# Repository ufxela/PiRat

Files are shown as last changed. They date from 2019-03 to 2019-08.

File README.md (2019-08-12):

# Pi Rat!

**Take a look at the video_links.md file in the images folder to see some videos 
of the robot in action!**

## Project Description

### Introduction
The Pi Rat is a robot that can solve a maze autonomously. It does this with two abilities: 
sensing and movement. Sensing comes through the form of an ultrasonic sensor (which is mounted
on a servo so it can look around) as well as a line follower module. The ultrasonic sensor
detects walls and the line follower module keeps the robot from veering off path (allows the robot
to go straight over long distances without hitting a side wall). The movement abilities come through 
two continuous rotation servos with hall effect sensors to provide rotational feedback. Each of these
has a wheel mounted to them, to create a differential drive car. Also, as I mentioned previously,
there's a servo which pans around to detect walls in combination with the utlrasonic sensor. 

The idea of the Pi Rat is to know as little information as possible about the maze. So far, I've been able
to eliminate the need for where the exit of the maze is, as well as any information about how the maze 
is set up. The information that I still require, and can be elimiated are the following: 
* The wall length / size of the maze
   * can be eliminated by sampling wall sizes with the ultrasonic sensor
* The dimension of the maze
   * With the basic wandering algorithm this actually isn't required information
* The starting position & bearing of the Pi Rat
* The need for a black line under each square of the maze to keep the Pi Rat from veering off path
   * Can use the ultrasonic sensor to measure where the Rat is relative to walls, in order to correct 
     position. Is more complex, however, than having black lines, as there won't always be walls present.

I had the idea for the Pi Rat during parents weekend, when I was talking with my mom and my
dad. My initial impression of the robot was pretty wrong. I thought that it would be able to 
maintain it's position well enough that I wouldn't have to have a line sensor.

Through this project, I've prided doing as much as I can by myself. It's meant that I've gotten the 
opportunity to learn new, unexpected things, like 3D modelling with CAD, laser cutting and 3D printing. 
I've also learned that I suck at painting (I can't paint straight, clean lines haha).

My junior year of high school, I tried to control servos with a Raspberry Pi running an OS. I quickly discovered
that this was not as straightforward as I would wish: apparently, the Raspberry Pi wasn't able perform time
sensitive actions well. I'm really glad that I've been able to come back to that and be able to control servos
with the Raspberry Pi with no extraneous hardware helping me.

### The Steps

The work I've done in this project can be broken down into bit sized steps. In approcimate cronological 
order for each category of work (I did software and hardware simultaneously): 

**Software**
1. Write a module to interface with the ultrasonic module 
1. Write a module to output pwm signals
1. Write a module to read pwm inputs
1. Write a module to control servos with the pwm output module
1. Write a module to control continuous rotation servos with the pwm output module
1. Write a module to interface with the line detecting sensor
1. Write a module to provide for basic differential drive car controls
1. Write a module to bundle all of the Pi Rat sensing into a single unified location
1. Write a module to bundle all Pi Rat movements into a single unified location, also add 
   movement correction, to ensure the Pi Rat is properly oriented
1. Write a module to use Pi Rat sensing and movement modules as well as maze solving algorithms
   to create functions which provide the robot with it's highest level of functionality
1. Combine everything neatly with a button which can be used to start / stop Pi Rat maze solving.

**Hardware**
1. Design Pi Rat robot chassis & 3D print it
1. Create a maze
   1. For portability, uses laser cut & self designed wall holder posts
   1. For walls, uses cut manilla folders which slot into wall holder posts
   1. For the ground, used a giant sheet of paper with a painted grid. 

### The Steps, in More Detail

**Software**
1. *Write a module to interface with the ultrasonic module:* This was relatively simple, doesn't 
   use interrupts. I referenced Pat's ultrasonic code. Initially, this function returned values in 
   inches. However, I wanted more accuracy, so I changed that to microseconds. One big issue I've had 
   with the ultrasonic sensor is the power line coming out, and making me think that my maze solving
   algorithms were broken. Make sure everything's plugged in!
1. *Write a module to output pwm signals:* This was one of the more challenging modules to write. I used
   interrupts to do it. My initial strategy was to step a timer up, and have thresholds where if a timer step
   counter was past that threshold, the output would switch. It ended up hogging up all CPU time, but I think
   it may be because I forgot to clear timer events. Regardless, I ended up switching to the current strategy
   of taking up 4 ms of every 20 ms of CPU time for a dedicated PWM output period. Bit banging. 
1. *Write a module to read pwm inputs:* This was an easy module to write initially, but some bad planning came
   back to bite me. The initial problem was that since pwm outputs hogged a big chunk of CPU time, if inputs
   clashed with outputs, bad things would happen. I fixed this by timing input reads around outputs. Another issue
   here was I forgot to ground things.
1. *Write a module to control servos with the pwm output module:* pretty straightforward, just tedious. 
1. *Write a module to control continuous rotation servos with the pwm output module:* A regret that I have is
   not leveraging the servo control module to make this. If I care enough in the future, I may fix this, but it
   functions perfectly right now. 
1. *Write a module to interface with the line detecting sensor:* Pretty straight forward, as I had the reference 
   from the manufacturer which included Arduino code. 
1. *Write a module to provide for basic differential drive car controls* This was one of the harder modules to
   write. The issue was that going straight means you need to move each wheel the same amount at the same speed.
   This is difficult when you use continuous rotation servos, which by nature are very inaccurate. Luckily, my
   continuous rotation servos had rotary encoders which made straight forward motion actually possible. However,
   I had to change my strategy for moving forward to a more complex one in order to get things working well.
1. *Write a module to bundle all of the Pi Rat sensing into a single unified location* Pretty straight forward. Uses
   a couple of different methods to filter through data from sensors, to make sure they're accurate. A problem is
   if a line is right in between two sensors of the line detector, it will hold indefinitely, or at least for a noticable
   time. This can be fixed with a better data getter function.
1. *Write a module to bundle all Pi Rat movements into a single unified location, also add* 
   *movement correction, to ensure the Pi Rat is properly oriented:* This module works really well in its current form.
   To correct forwards motions, it corrects any lateral error as well as angular error based on a measurement it makes 
   before movement as well as a measurement it makes after movement. To correct turns, the Pi Rat will turn, then fix the
   lateral error. These corrections are really nice because it allows for a lot of leeway in the maze design. For example,
   walls don't all have to be the perfect size, as after each turn, any error should be corrected. Furthermore, the turns
   don't have to be perfectly 90 degrees, as the forwards motion correction will soften offsets.
1. *Write a module to use Pi Rat sensing and movement modules as well as maze solving algorithms*
   *to create functions which provide the robot with it's highest level of functionality:* This was the final step
   in my mind, and used my cs106b maze solving knowledge.
1. *Combine everything neatly with a button which can be used to start / stop Pi Rat maze solving:* icing on the cake; to
   the in class demonstration a lot more approacable to interaction. 

**Hardware**
1. *Design Pi Rat robot chassis & 3D print it:* Went through three iterations of design. The first did not account
   for the line follower, as I didn't expect to need it. The second fixed this and the third added additional supports
   between the top and bottom pieces to make the fit cleaner. I really liked the way my chassis turned out. My idea
   behind it was to make it as small as possible, so I could make the maze size as small as possible. I also didn't want
   anything permanent, so there's no glue holding anything together: everthing is friction fit (well, wires are taped down).
   Some things just worked out in the design, like routing the continuous rotation servo's wires, or making sure the 
   wheels fit in the chassis. Also, I got to learn (well, sorta...) fusion 360. I don't say that confidently because all
   I did was make a bunch of rectangles and extrude them to various heights. 
1. *Create a maze:* In fashion with the rest of my project, I wanted to complete this myself. I also wanted it
   to be portable, for convenience. 
   1. *For portability, uses laser cut & self designed wall holder posts:* I designed these in fusion 360, and discovered
   that laser cutters are really scary. I also had to assemble the flat pieces into non-flat structures. I used a lot
   of hot glue for this.
   1. *For walls, uses cut manilla folders which slot into wall holder posts:* Manilla folders are actually an amazing
   building material. I got a bunch super cheap for their conventional purpose, but I had extras, so why not put them to use?
   Fun fact: I prototyped a chassis with only manilla folders, tape and hot glue. 
   1. *For the ground, used a giant sheet of paper with a painted grid:* I painted this, using long manilla folder
   strips to make sure I didn't paint in the wrong places. That ended up not really working because paint got on the
   bottom of those strips, and ended up spreading paint all over, including on my body. As a result, I had to use white paint
   to cover all the black blotches that weren't supposed to be there (on the maze, not my body... thankfully the paint was
   easily washable). 

### The Product
The end result of all of this work was that I had a Pi Rat that can solve a maze in two ways!

The first way is with a really basic algorithm which follows this procedure:
`
for each direction:
  if open:
    go that direction
    recur
`
The nice thing is that this algorithm needs very little information about the maze. The bad thing is that it doesn't work
always. To use this, just call the maze wander function, place the rat in the maze, and watch it solve the maze!

The second way is with a depth first search. This algorithm needs a little more information about the maze, like
where the Pi Rat starts in the maze, and the dimensions of the maze. It always works when there is a path, however. To use 
this, update some constants in main.c (as well as wall lengths in the car control module), then call the maze solver
function and watch as the Pi Rat solves the maze!

The program is for the most part modular: by chaning a few constants, the maze solving is generalizable to 
any rectangular maze of any dimensions, configuration and wall length!

[Video Links!](https://github.com/cs107e/ufxela-project/blob/master/images/video_links.md)

### Pictures! (A Lot More in Images Folder)
The Maze:
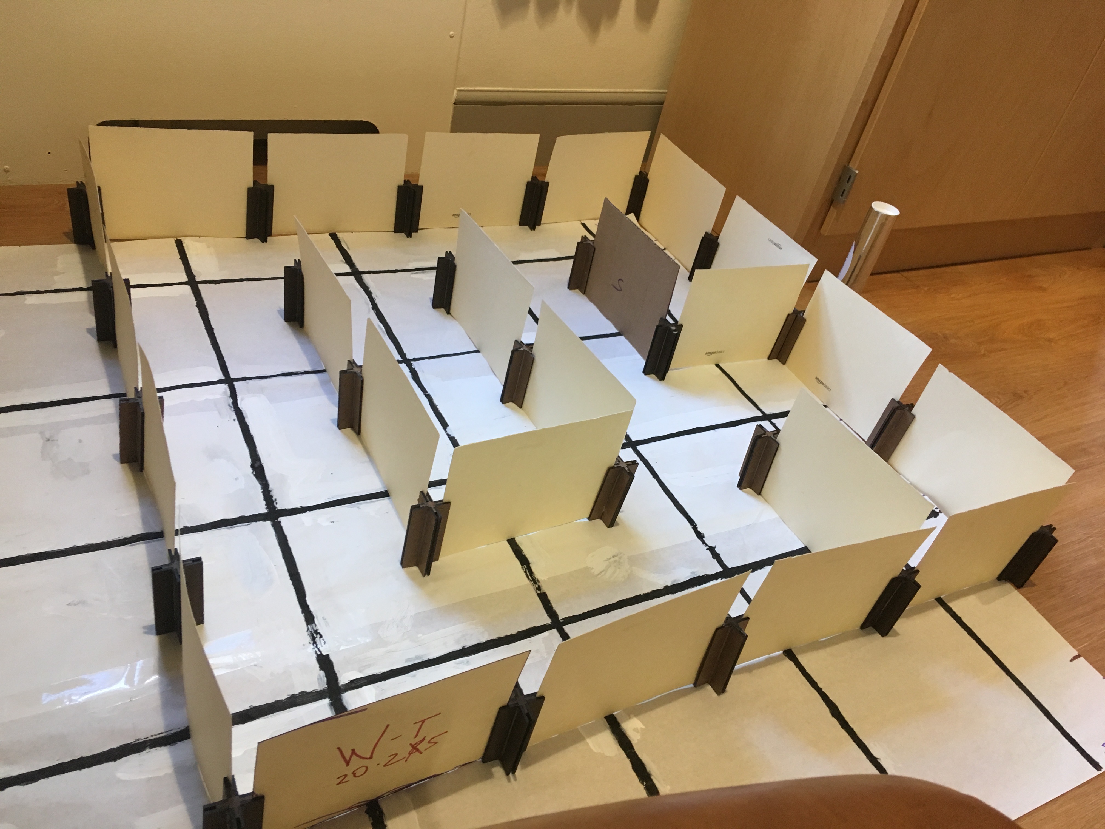
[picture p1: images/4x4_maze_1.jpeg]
The Maze

Another Maze:
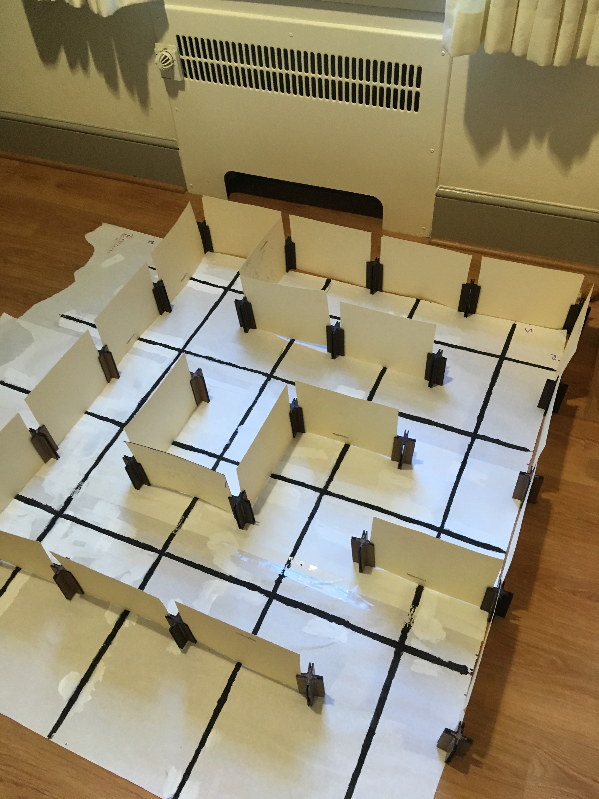
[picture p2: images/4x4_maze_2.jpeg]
Another Maze

The Maze, deconstructed
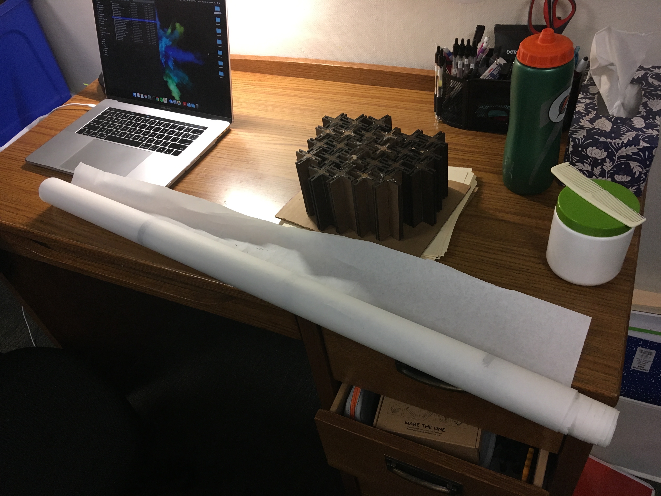
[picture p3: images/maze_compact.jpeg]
Deconstructed Maze

The Pi Rat: 
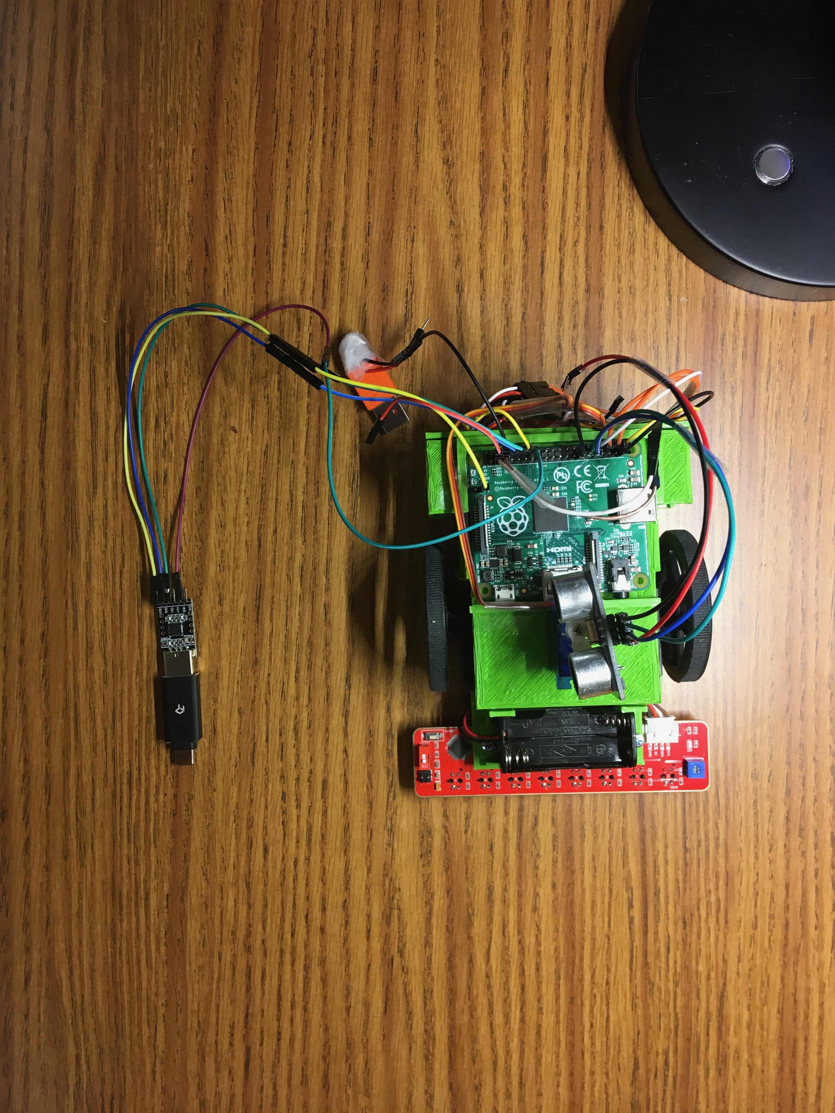
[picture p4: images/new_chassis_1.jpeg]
Pi Rat 1

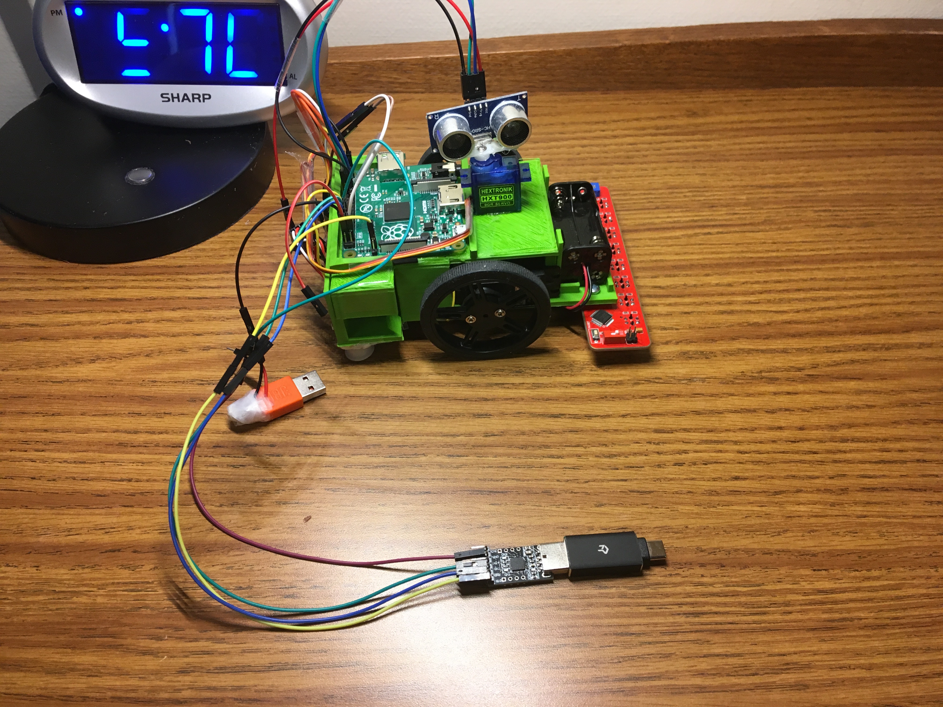
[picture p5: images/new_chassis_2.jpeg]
Pi Rat 2

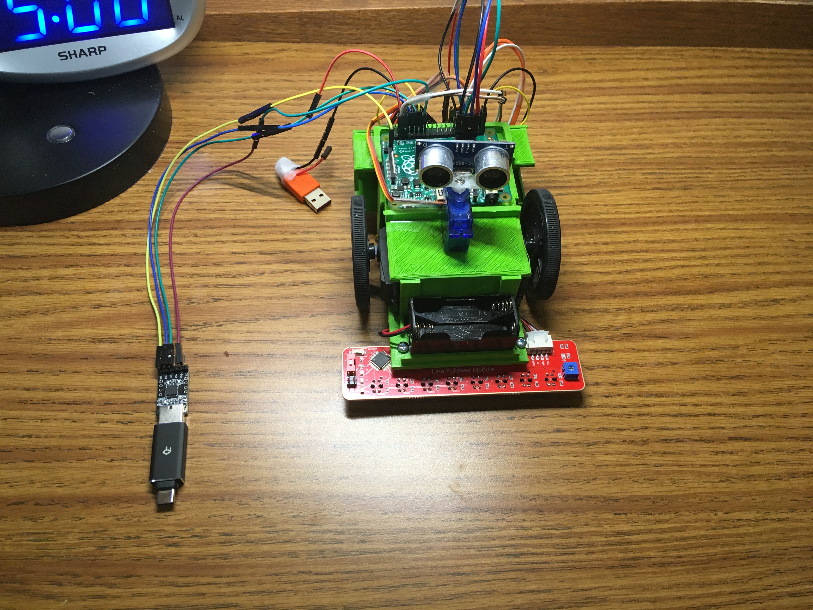
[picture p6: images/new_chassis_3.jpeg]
Pi Rat 3

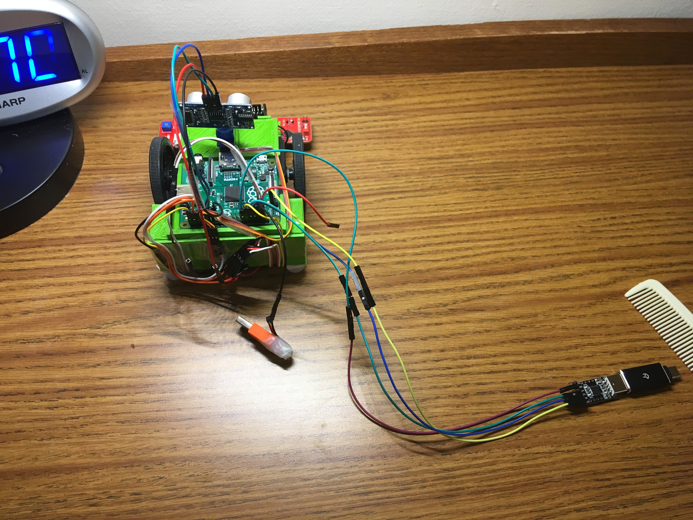
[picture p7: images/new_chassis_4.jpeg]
Pi Rat 4

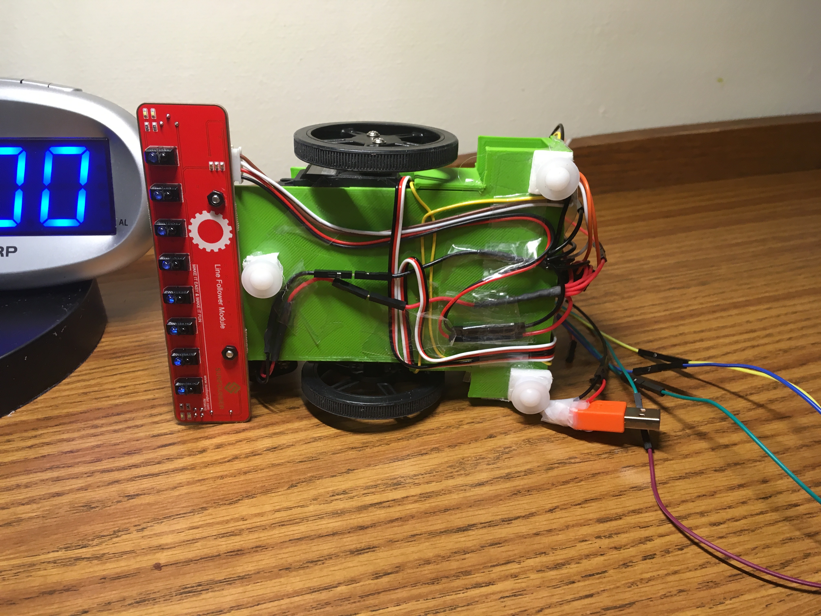
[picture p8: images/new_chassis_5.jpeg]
Pi Rat 5


## Notable Challenges
1. *PWM Outputs:* This was a big hurdle. My first implementation of PWM outputs failed. It seemed to hog all the CPU time.
  I now relaize that I probably wrote it wrong (forgot to clear timer events). I haven't had the effort to check if this is
  why, since the current version works. However, the reason I think this is because, when set to have cycle length 20ms, 
  the actual cycle length turned out to be ~7ms (measured with a logic analyzer). I think this is because the interrupt 
  handler was just being called nonstop. Once I did switch to the current implementation of the code, however, the servos
  still weren't working, even though the logic analyzer showed valid PWM signals. Initially, I thought this was because
  the signals weren't precise enough. However, it turned out that it was because I didn't connect all of my grounds. 
  Throughout the process of solving PWM outputs, Pat helped me a lot. One suggestion he gave me was to use a task queue, which
  although I didn't end up implementing, inspired me to switch to the current implementation of PWM. 
1. *PWM Inputs:* While solving PWM outputs, I reached a point where I felt I was in too deep and couldn't think freshly any
  more, so I switched to solving PWM inputs. My initial implementation of these worked, and I was super excited! Then,
  fifteen minutes later, with no changes to the code, I tried again, and it had stopped working! This was heartbreaking,  
  especially since I wasn't able to get PWM outputs to work. I spent an hour digging through the code, seeing what might
  have gone wrong. This didn't lead anywhere. Then had the idea to physically reconstruct my successful setup exactly,
  to see if that would change anything. It did! It turned out that I didn't connect my ground lines properly. That was
  one of the most confusing hours of this project, and one of the most frustrating.
1. *Going straight & accurately reading wheel positions* These two problems were highly entangled. My inital wheel position
  reader was very imperfect. I regularly got very wonky data from the pwm input reader. My inital strategy to solve this
  was to just deal with it by adding in data filters. This gave limited success, but every once in a while, there was an edge
  case of bad data which would break everything. This meant the wheels would track well for maybe a minute of movement, but
  break after that. I could have added more filters to cover more and more edge cases. Maybe I could have even gotten a 
  perfect filter. However, my filtering code was only getting longer and more convoluted. The right way to do things was to
  dig into the PWM inputs and see why they were so wonky. Once I solved that, I didn't need any filters, and my code worked
  better than ever, with more simplicity than ever. Inaccurate wheel positions also meant that my movements were all wrong.
  At the time, I was simply trying to perfect straight forward movement, so we'll focus on that. My initial implementation of
  forward movement was to spin each wheel independently to a set angle, and assume that each wheel was spinning at the same 
  speed. This failed initially because the poor wheel tracking meant I couldn't consistently bring a wheel to a given angle, 
  without "rotation count slipping" which caused wheels to turn a few rotations too much or too little. Once I solved
  the wheel angles, I thought that would solve the issues with my forward motions. They did not. Although each wheel was set
  to spin a different amount, each wheel span at a different rate, which meant at the end of the motion, one wheel would stop
  and the other would continue spinning. This lead to turning. So I decided to switch to a different, more complex forward
  motion function, which made the wheel throttles dependent on eachother's angles. This worked, after some fine tuning.
  It goes to show that not everything is as simple/straightforward as you may initially think.
1. *DFS maze solver:* Unfortunately, this was not as simple as 106b, mostly because of my own fault. In 106b, our mazes
  had walls being area containing squares, instead of one dimensional lines. We also had better data structures. We also
  didn't have to physically move an object and worry about that. Nor did we have to sense the environment as we went. Now,
  I know I could have written more layers of abstraction early on to resolve these differences. But I am naive and didn't
  anticipate these issues coming up. As a result, my code is very verbose, has some arms length recursion, and is pretty ugly
  overall. Furthermore, I had one big bug in my first draft of the code that took me a while to figure out. The bug was that
  I didn't update the position of the Pi Rat enough, which meant it often thought it was in the wrong spot. As a result,
  when testing, the Pi Rat would seemingly ignore certain paths (and presumably, I'd see it run into walls, if I tested it on
  more mazes). This bug would be simple to fix if everything was simulated on my computer. However, since the Pi Rat was 
  physically solving the maze, visibility of the code and program was terrible while the Pi Rat was in the process of solving
  the maze. This is because while the Pi Rat was solving the maze, it couldn't communicate with my computer and therefore,
  I could only speculate as to what it was thinking. To solve this, I spent a couple of hours playing around with the code
  and then re testing, true to a trial and error approach. However, since I had no idea what the Pi Rat was thinking, this
  was very difficult and ultimately unsuccessful (it did get me closer to the end solution, however). Eventually, I 
  succumbed to using extra long jumper wires to connect the Pi Rat to my computer, and then I basically "walked" the Pi Rat
  by following it through the maze with my computer that was connected to it. It was a funny sight to see, but it worked. I 
  was able to get the data I needed to tell me what I was doing wrong (not updating enough). 

In summary, the hardest part of this assignment was definitely visibility & understanding the hardware.

## Things learned
1. Planning is critical, and possibly the most difficult part of it all. Many modules were easy to implement, aside from
  a few roadbumps (like the ones I talked about above). The hard part was finding the right order to write them in and 
  determining what modules to even have, and what to have inside them. 
1. Do things in the right order: you may find yourself in a situation where you can either
  write tests to debug and make information more transparent and make the mechanisms behind
  things more visible, or you can try to brute force things and try to solve things without 
  that information helping your strategy. Sometimes the latter is faster. However, other times 
  it is not, and it can get very frustrating, because you just feel like you don't know what is
  going on. I have more appreciation for the advice that it's worth your time to write tests
  and make code more visible. Even if it takes 30 minutes, it will save your butt later.
1. Don't change things at the last minute, and if you do, be sure to verify that they don't break anything. The night before the project demos, I did some code cleanup, and ended up changing the Pi Rat's internally kept starting position. This meant that when I placed the Rat in the maze, it thought it was somewhere other than where it actually was. This meant that it thought it solved the maze when really it hadn't. And so the project demo did not go as planned, unfortunately. 
1. Some other things I learned are in my proposal

## Extensions
There were a few things that I had ideas for, and wanted to implement if I had the time, but I never ended up getting to them

Here are a few of them:
1. Remove more information about the maze. I talked more about this above.
1. Make a better interface to the Pi Rat. What if the user could tell the Pi Rat where it's start position should be, 
  with just buttons or something? What if the Pi Rat could display information on a 7 segment display or screen?
1. More maze traversing options: go from point A to point B once a maze is mapped out; after a maze is solved, continually
  traverse the optimal path from start to finish.
1. Remove the line follower sensor completely. Instead use the ultrasonic sensor for all orientation corrections.
1. Move past just mazes and into rooms. Explore a room, kind of line a Roomba. Maybe even keep track of
  data about the room. A simple version of this would be really easy to make. 
1. Remote control abilities, maybe over WiFi?
1. Make a white board robot. I have all of the hardware setup to do this.

## Files
1. Images is a folder which includes photos & a markdown file video_links.md to video links
1. 3d wall plate pi rat maze.stl is a stl file for my wall holder plates. I cut 200 of these out
   (25 wall holders * 8 plates per holder)
1. 8x pi rat maze wall plates.dxf is the file I opened with inkscape on Lab 64's laser cutter computer
   Note that you might need to delete some lines, as some are doubled up (my bad).
1. Chassis_Bottom.stl is the part I 3D printed to make the bottom half of the chassis. I'm not currently
   using this one. 
1. Chassis_Top.stl is the final part I 3D printed to make the top half of the chassis
1. Makefile is self explanatory
1. README is this!
1. better_bottom_chassis.stl is the final part I 3D printed to make the bottom half of chassis
1. car_control_module.c/h provide for basic, non corrective car movements for a differential drive car.
   They use cr_servo_module.c/h and pwm_input_module.c/h
1. cr_servo_module.c/h control continuous rotation servos. Uses pwm_output_module.c/h
1. cstart.c is some code that sets a few things up and calls main
1. libmypi.a is the library I wrote for the first 8 weeks of cs107e
1. line_follower_module.c/h is the module which interfaces with the line follower hardware over i2c
1. main.c is the centerpiece of the program. Contains a lot of test code. 
1. memmap is for linking
1. pi rat maze bottom:top plate 3d.stl is the 3d version of the top/bottom plates of wall holder
1. pi rat maze top:bottom plate.dxf is the inkscape openable file I used to laser cut the wall holder 
   plates
1. pi_rat_control.c/h implement different control functions. Uses pi_rat_movement.c/h and 
   pi_rat_sensing.c/h 
1. pi_rat_movement_module.c is the corrective movement module which moves the car in a way which is 
   specific to the setup of a given maze. Uses car_control_module.c/h and pi_rat_sensing.c/h
1. pi_rat_sensing_module.c/h combines ultrasonic_module.c/h and line_follower_module.c/h into one
   centralized module
1. proposal.md was the description that I wrote up on the first lab for this project, and added to
   as I was working in the first week.
1. pwm_input_module.c/h read in pwm signals through interrupts. Uses pwm_output_module.c/h for proper
   timing
1. pwm_output_module.c/h output pwm signals using timer interrupts
1. servo_module.c/h use pwm_output_module.c/h to make a more intuitive servo control library
1. start.s is the first file that gets called when running
1. ultrasonic_module.c/h interface with the ultrasonic sensor. 
1. updated_bottom_chassis.stl was an internediary between my original bottom chassis and the one I used

## Team member work outline
I did it all myself (with the advice of others, listed below, of course)!

## Resources/Citations

Pat's ultrasonic sensor [sample code](https://github.com/cs107e/cs107e.github.io/blob/master/lectures/Sensors/code/sonar/sonar.c) 

-I used this to get the conversion from microseconds to inches.

[Pseudo code](http://www.robotc.net/wikiarchive/Tutorials/Arduino_Projects/Mobile_Robotics/VEX/Using_encoders_to_drive_straight) for forward motion with wheel angle feedback.
 
 -just followed the pseudo code, adding in limits for wheel throttles and fine tuning for my car

Line follower [example code](http://wiki.sunfounder.cc/index.php?title=Line_Follower_Module)

-borrowed the code pretty much directly

[i2c code](https://github.com/cs107e/cs107e.github.io/blob/master/cs107e/src/i2c.c) to communicate to line follower module

Thanks to Ashwin, Jennifer, Julie, and Pat for providing confidence inspiring guidance throughout my project!

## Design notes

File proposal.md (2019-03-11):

# Pi Rat

**Team members:** Alex Fu

**Description:**
PiRat is loosely inspired by Tolman and Honzik’s psychology experiments (1930) 
in which a live rat was placed in a maze and given the task to find a reward 
(stereotypically cheese) within the maze. PiRat will model the rat, and attempt 
to solve a maze given little prior information about the structure of the maze.

PiRat will have two primary abilities: the first is the ability to move around.
The second is to sense its environment. To move around, the Pi Rat will utilize
continuous rotation servos and a rotary encoder. To sense its environment,
the Pi Rat will use a dinstance sensor (either ultrasonic or time of flight). The
Pi Rat will also use a line sensor to keep it's position/orientation correct, so
that it does not stray off the path and run into the sides of the maze. 

With these two abilities, the PiRat can use a depth first search path finder 
algorithm to navigate through a maze, and find a solution. At the same time, 
the PiRat will keep an internal model of the maze, updating the model with each 
measurement it takes with it’s ultrasonic distance/time of flight sensor. 

One challenge of this project is keeping the Pi Rat's orientation correct throughout
the maze. Because the Pi Rat senses very little about it's environement, it is difficult
for it to truly know where it is (position and bearing) within the maze. Therefore, small
inaccuracies in positioning can avalanche to throw the entire Pi Rat off track. 

**Hardware Required:** 
besides a Raspberry Pi,

* 2x parallax feedback 360 servo motors
* 1x time of flight sensor / ultrasonic distance sensor
* 1x 9g servo
* 1x Line Follower Module
* 3D printed chassis
* 2 wheels, good grip (no slipping!)
* free wheel / low friction knob
* cardboard / foamboard to build maze

**Funds Requested:**

* Optical Time of Flight Sensor: 
    * https://www.amazon.com/Adafruit-VL6180X-Flight-Distance-Ranging/dp/B01N0ODI3Q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
    * $13.99
* 9g servo
    * https://www.amazon.com/DaFuRui-Compatible-Helicopter-Airplane-Controls/dp/B07H3S2Y8Q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
    * $7.89
* Line Follower Module 8 Channel Infrared 
    * $12.99
    * https://www.amazon.com/SunFounder-Follower-Infrared-Detection-STM8S105C4/dp/B01HB5YVUG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
* **Total**
    * $34.67 (but I have a $10 amazon credit!)

**Task Breakdown**

*Software:*

1. Write a module to output PWM signals
1. Write a module to read PWM inputs
1. Write module to setup and control a servo through PWM
1. Write module to setup and control continuous rotation servo through PWM
1. Write module to read PWM communications from Parallax Feedback 360 servos, to determine positioning
1. Either:
   1. Communicate through I2C to optical time of flight sensor
   1. Read/write through GPIO to communicate with ultrasonic distance sensor (This is what I have chosen).
1. Write module to communicate via I2C with the line follower module
   1. Will use libpiextra i2c modules
1. Module to move support basic movement of a continuous rotation servo powered car.
   1. With two independent wheels, we will be able to move forward, backward, turn and shimmy to the left and right
1. Module to support advanced movement for Pi Rat
   1. Will keep track of position of Pi Rat
   1. Will have discretized movements so as to follow maze properly
   1. Will have correctional movements that ensure proper orientation within maze (no roaming off track)
1. Code to use all modules to sense environment and move the rat in response based on
   where it wants to go. 
   1. Internal data structure to represent maze
   1. Algorithm to solve maze
   1. Internal data structure to represent current path, and provide ability to backtrack path.
   1. Way to determine when solution is discovered
   1. Traverse solution (back and forth, like a sentry) once found. 
   1. Once maze map is completed, user may tell Pi Rat to go from point A to point B for any two connected
      points in the maze.
   1. User may input instructions to the Pi Rat beforehand to tell it where to go
1. Extensions:
   1. Code to use modules to traverse a new environment that may not be a maze. 
   1. Code to find shortest path from point A to point B within maze. 
   1. Remove any information about the maze at all (step size, dimensions) and use Pi Rat's sensing abilities
      to determine this information itself. 
   1. Add in remote control abilities. 
   
*Hardware:*

1. Model and 3D print chassis for rat
1. Mount time of flight sensor / ultrasonic distance sensor
1. Mount line follower module
1. Find / make wheels which have really good grip
1. Make maze, ideally with configurability. (slot and fit walls)

**Goals for Next Week**
1. Software steps 1-7
1. Hardware steps 1-4
1. Test movement of Pi Rat and see how accurately it can hold its position
1. Test accuracy of ultrasonic sensor
1. Configure servo motors
1. Configure line follower sensor

**Reference and Resources**

*another document that goes into more detail about my project*

https://docs.google.com/document/d/10EH3p42lqzU2tbl3T3y5yWcG4yZZ02CRSOTUqFnZRl0/edit?usp=sharing

*line follower*

http://wiki.sunfounder.cc/index.php?title=Line_Follower_Module
https://github.com/cs107e/cs107e.github.io/blob/master/cs107e/src/i2c.c
Note: this bad boy can't be powered just through the Pi's GPIO pins. Needs external supply!

*ultrasonic sensor*

https://cdn.sparkfun.com/datasheets/Sensors/Proximity/HCSR04.pdf
https://github.com/cs107e/cs107e.github.io/blob/master/lectures/Sensors/code/sonar/sonar.c

*parallax feedback 360 servos*

https://www.parallax.com/product/900-00360

*servos*

https://learn.sparkfun.com/tutorials/pulse-width-modulation/all

*CS107E Libraries*

https://github.com/cs107e/cs107e.github.io/tree/master/cs107e/src
https://github.com/cs107e/cs107e.github.io/tree/master/cs107e/include

Specifically: gpioextra, interrupts, i2c. 

*Wheels*

The wheels that I'm using are borrowed from this kit: https://www.amazon.com/Geekstory-Feetech-Degree-Continuous-Rotation/dp/B079FRHBTR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

**Lessons that I have Learned**
* Have only one ground. Otherwise, you will pull your hairs out.
* Line follower module needs to be powered externally
* At first glance, things will seem definitely doable. Then once you start doing them, they no longer seem doable.
  But once you complete them, they seem very doable.
* Object oriented programming can be very helpful, but not if you don't do it. I should do it more often in my coding.
* There is a lot more to consider besides the software side of things. For example, an uneven weight distribution
  in the chassis will lead to one wheel having more grip than the other. So have an even weight distribution.
* Many things pop up and make other things hard. For example, keeping the orientation of the Pi Rat correct throughout the
  maze. You have to constantly figure solutions out to these challenges. Many of the best solutions come in the shower.
* Oftentimes, things are difficult because you make them so. It can be good to take a step back, and think: is there a 
  simpler, easier solution to things? This is difficult because you can get caught up in the way you currently want to
  do things, and miss out on otherwise obvious things. For example, when writing PWM outputs, initially I picked up Pat's
  idea (which, now that I look back, should work, if I properly used get_and_clear_event()...) with the incrementing interrupt
  counter. But later, I took a simpler, better approach which is currently implemented. Also, with utilizing the line
  follower, my initial thought was to update the orientation as the Pi Rat moved. But then I realized it would be much 
  simpler if I compartmentalized each operation. First move, then correct the movement. 
* This brings me to: compartmentalizing things means you can do so much more. "Stand on the shoulders of giants" except
  In this case, you are the giant. There are so many details of my code that are critical but I've totally forgotten about
  (well, I could recall them, but it's much easier not having the worry of needing to). And by leaking those details from my
  memory, I've allowed myself to use my mind more completely to solve each task. Whereas, if I chose to mesh everything
  together, either I would be able to do much less in coding, or I would have to spend way more effort achieving it. This
  is part of the reason I chose not to use a task queue for control, and instead opted to compartmentalize PWM outputs, even
  if it meant having that 2-3 ms penalty. 
* When you're doing something completely alone, that you really enjoy, there really is nothing else needed. Although I've
  been really frustrated at times (like before I realized you should connect all your grounds--lesson learned!), and I've
  definitely wished that I had someone along side me helping me solve my problems (in a way, I have--through the course staff)
  but at the end of the day, I'm really glad to have embarked on this project. It's definitely overwhelming. But worth it.

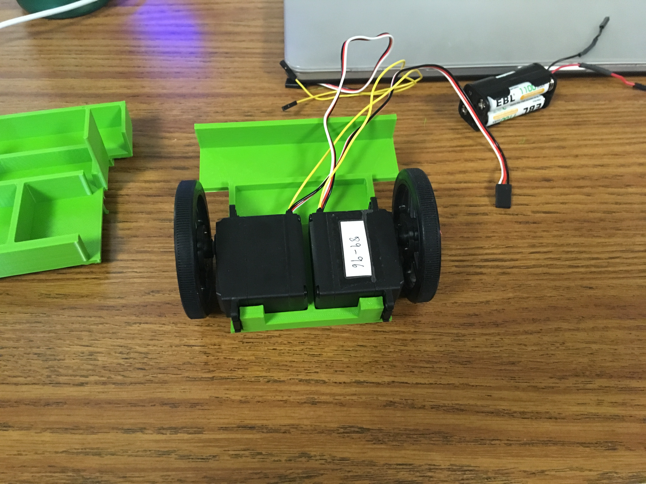
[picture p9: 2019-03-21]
images/friction_fit_chassis_motors.jpeg

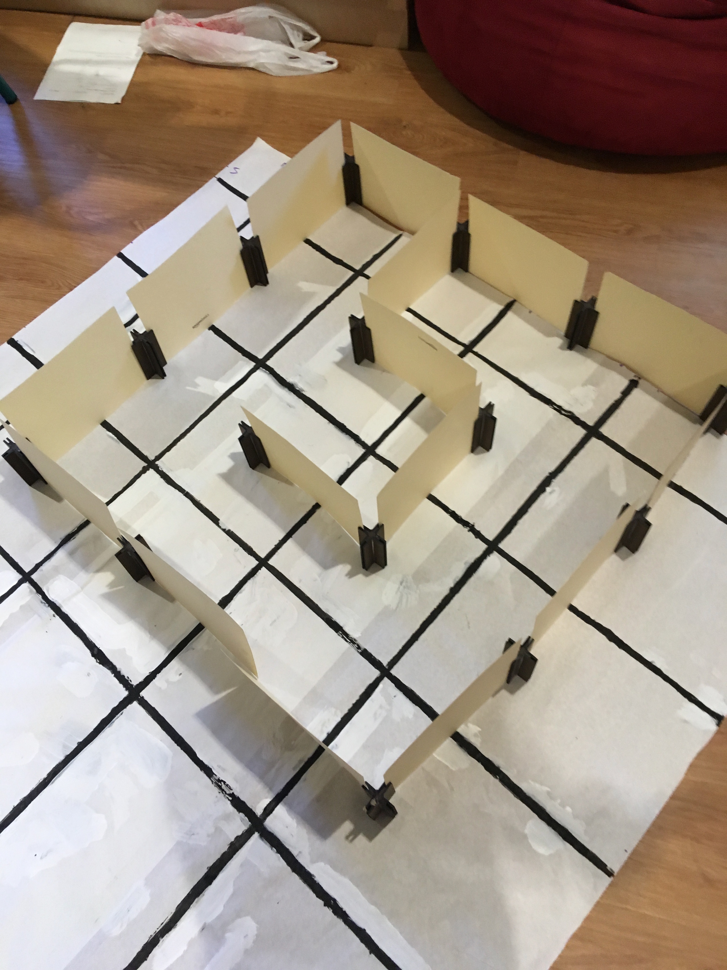
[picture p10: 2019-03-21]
images/3x3_maze_1.jpeg

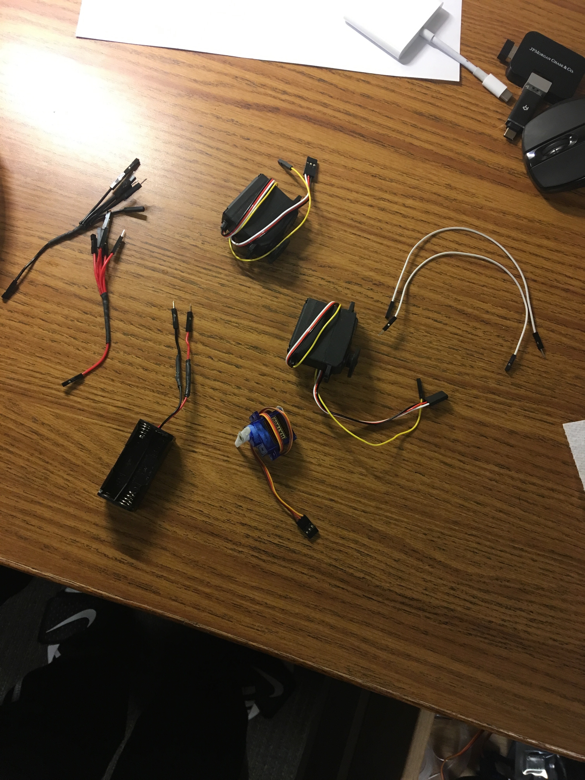
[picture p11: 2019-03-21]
images/motors.jpeg

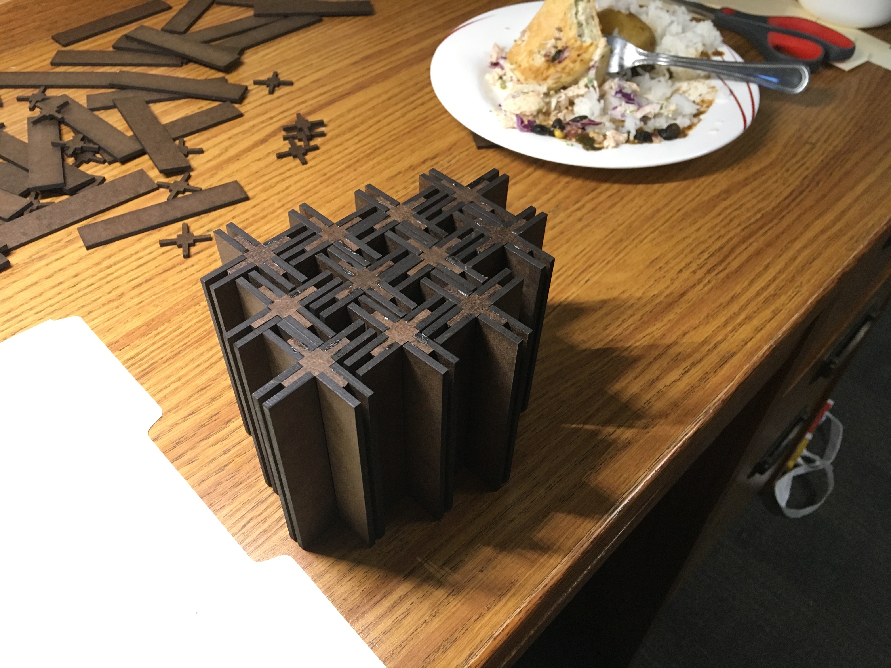
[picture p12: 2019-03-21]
images/wall_posts_1.jpeg

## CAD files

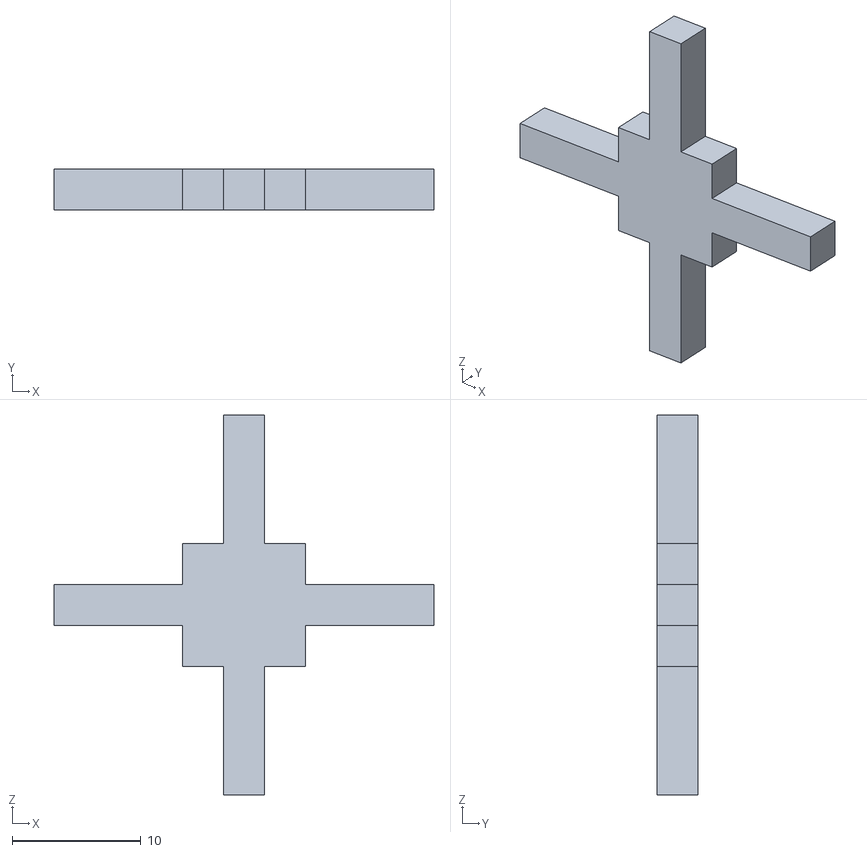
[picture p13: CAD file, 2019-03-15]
pi rat maze bottom:top plate 3d.stl
29.5 x 3.17 x 29.5

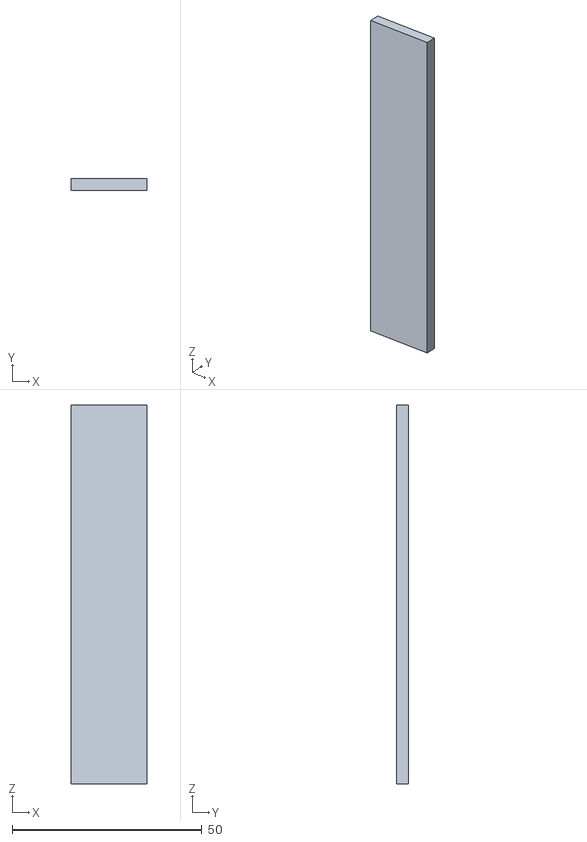
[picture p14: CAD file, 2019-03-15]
3d wall plate pi rat maze.stl
20.0 x 3.17 x 100.0

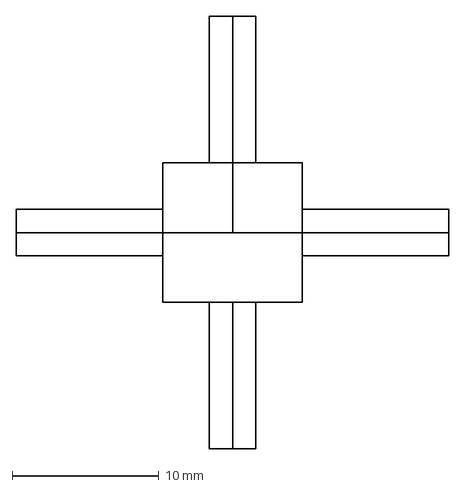
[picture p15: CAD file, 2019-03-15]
pi rat maze top:bottom plate.dxf
29.5 x 29.5 mm

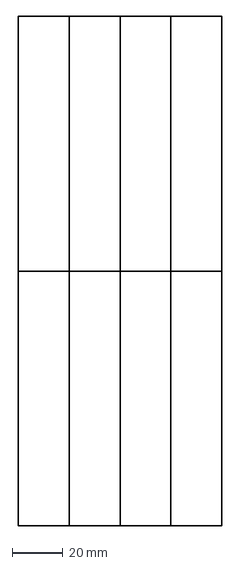
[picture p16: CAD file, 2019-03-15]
8x pi rat maze wall plates.dxf
80.0 x 200.0 mm

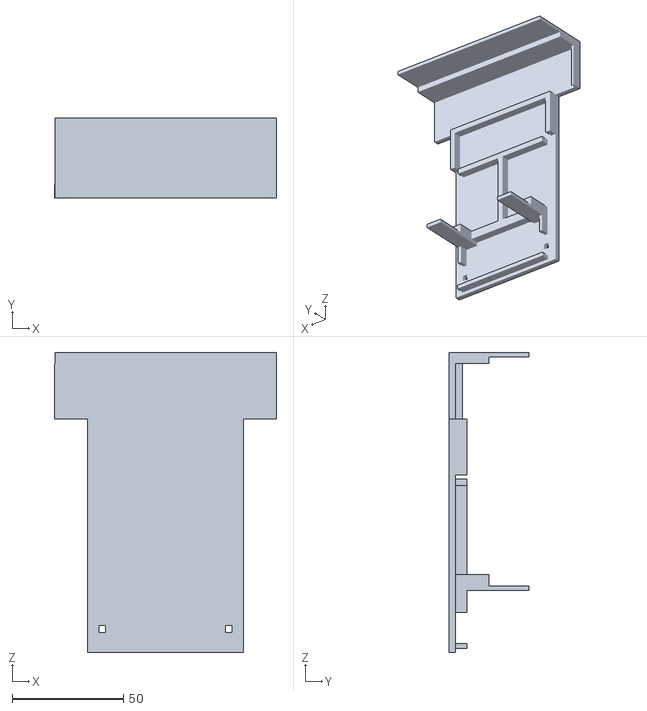
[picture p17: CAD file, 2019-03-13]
better_bottom_chassis.stl
100.0 x 36.0 x 135.0

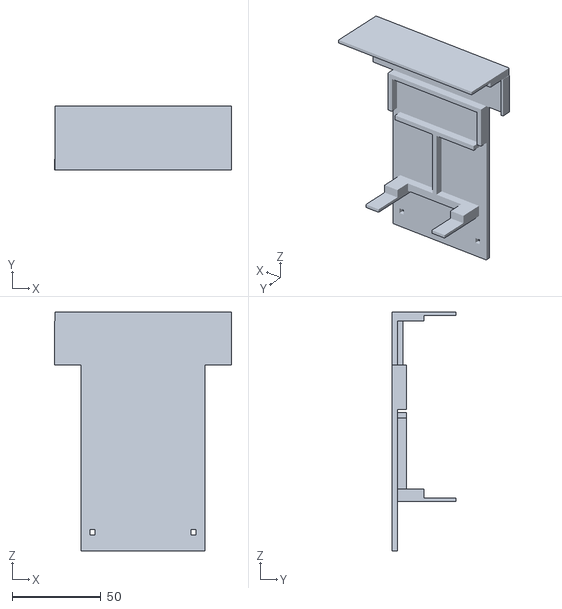
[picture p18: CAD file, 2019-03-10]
updated_bottom_chassis.stl
100.0 x 36.0 x 135.0

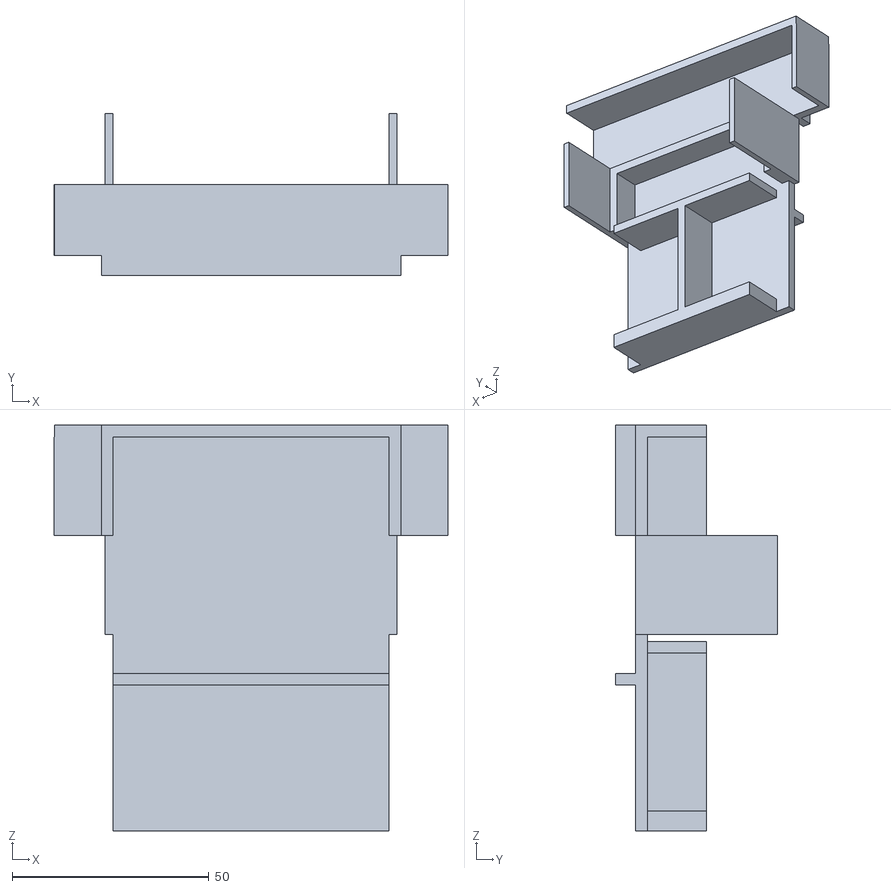
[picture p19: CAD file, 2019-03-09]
Chassis_Top.stl
100.0 x 41.0 x 103.0

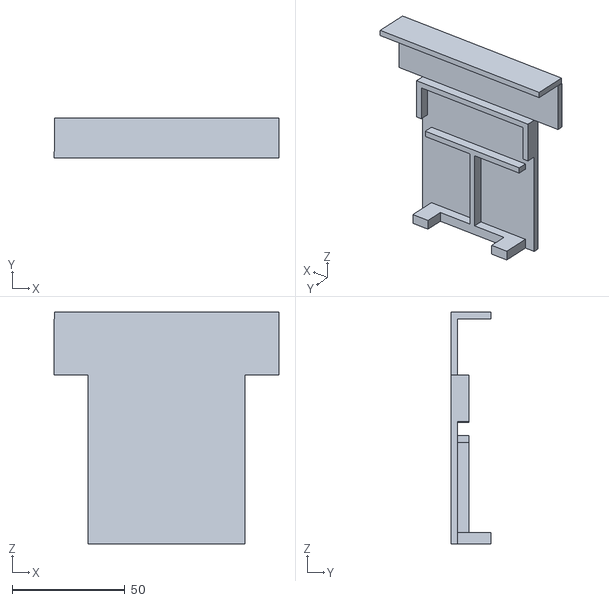
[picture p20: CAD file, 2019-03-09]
Chassis_Bottom.stl
100.0 x 18.0 x 103.0

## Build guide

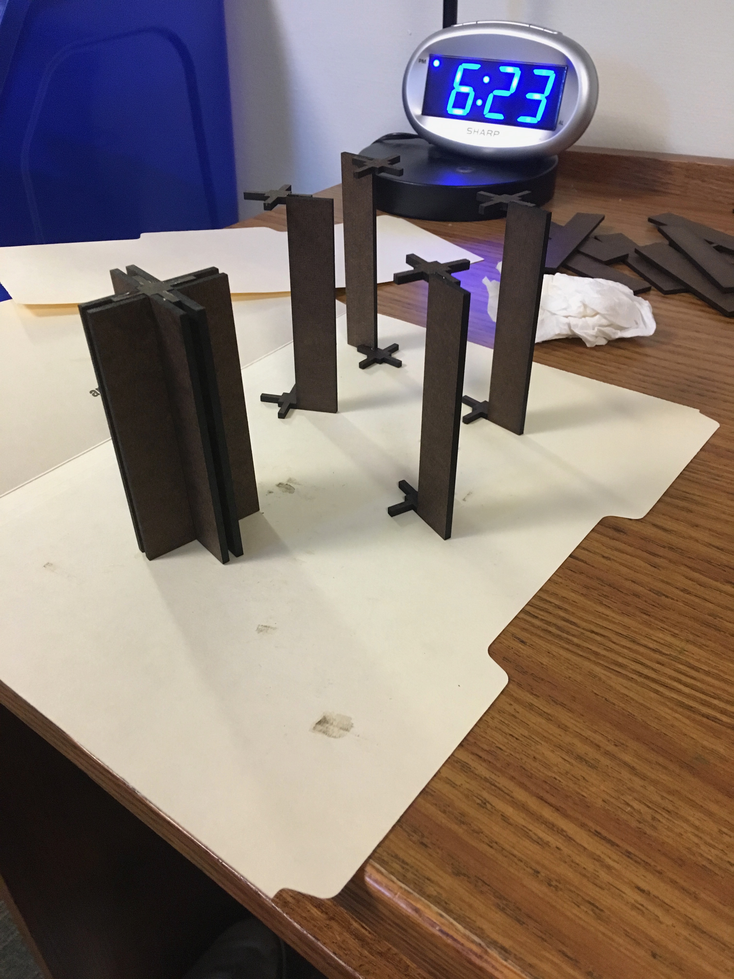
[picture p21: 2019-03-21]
images/wall_post_assembly_2.jpeg

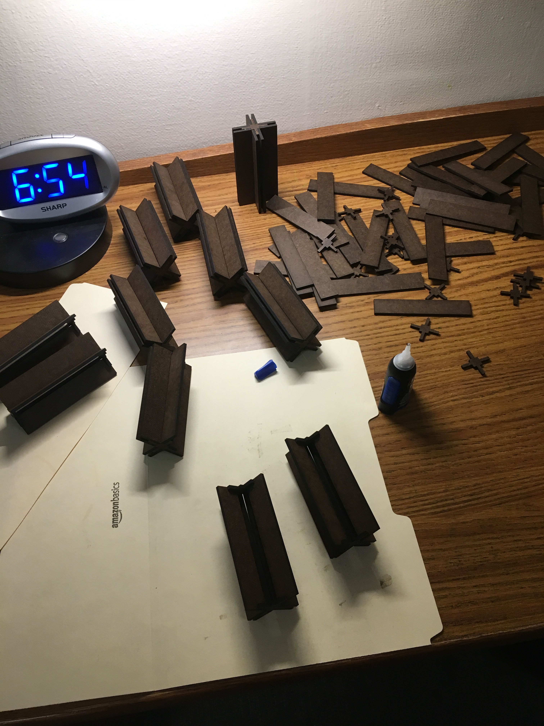
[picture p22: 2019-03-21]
images/wall_post_assembly_1.jpg

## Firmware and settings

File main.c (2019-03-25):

/* this is the primary program of this repository
 * which is the command central, and everything is being called from here
 * includes a lot of test programs to verify functionality of modules
 */

#include "printf.h"
#include "uart.h"
#include "ultrasonic_module.h"
#include "timer.h"
#include "gpio.h"
#include "pwm_output_module.h"
#include "pwm_input_module.h"
#include "servo_module.h"
#include "cr_servo_module.h"
#include "car_control_module.h"
#include "line_follower_module.h"
#include "pi_rat_sensing_module.h"
#include "pi_rat_movement_module.h"
#include "pi_rat_control.h"
#include "gpioextra.h"
#include "interrupts.h"

const unsigned int ULTRASONIC_TRIGGER = GPIO_PIN6;
const unsigned int ULTRASONIC_ECHO = GPIO_PIN5;
const unsigned int RESET_BUTTON = GPIO_PIN13;
const unsigned int START_X = 0;
const unsigned int START_Y = 0;
const unsigned int START_BEARING = 1; //start facing forwards
const unsigned int END_X = 5; //invalid so that maze will search for any opening
const unsigned int END_Y = 5;
const unsigned int MAZE_DIMENSION_X = 4;
const unsigned int MAZE_DIMENSION_Y = 4;
const unsigned int IN_1 = GPIO_PIN18; //first motor input pin
const unsigned int IN_2 = GPIO_PIN21;
const unsigned int OUT_1 = GPIO_PIN20;
const unsigned int OUT_2 = GPIO_PIN16;
const unsigned int PAN = GPIO_PIN12;

/* if button is pressed, then wait for ten seconds, and then start solving the maze again */
static bool button_press(unsigned int pc)
{
  if(gpio_check_and_clear_event(RESET_BUTTON)){
    printf("10 seconds until we start again");
    timer_delay(10);
    printf("solving maze now");
    pi_rat_reset();
    return true;
  }else{
    return false;
  }
}

void button_init(void)
{
  gpio_init();
  gpio_set_input(RESET_BUTTON);
  gpio_set_pullup(RESET_BUTTON);
  gpio_enable_event_detection(RESET_BUTTON, GPIO_DETECT_FALLING_EDGE);
  interrupts_attach_handler(button_press);
  interrupts_enable_source(INTERRUPTS_GPIO3);
  interrupts_global_enable();
}

int main(void)
{
  uart_init();
  timer_init();
  button_init();
  /* test the maze solver on a 4x4 maze */

  printf("beginning maze solving in 7 seconds \n");
  timer_delay(7);
  pi_rat_init(IN_1, IN_2, OUT_1, OUT_2, ULTRASONIC_TRIGGER, ULTRASONIC_ECHO, PAN);
  while(1){ //loop so that once we finish and the button is pressed, it will begin again
    pi_rat_solve_maze(START_X, START_Y, START_BEARING, END_X, END_Y, MAZE_DIMENSION_X, MAZE_DIMENSION_Y);
  }
  return 1;
}

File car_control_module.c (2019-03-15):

#include "car_control_module.h"
#include "pwm_input_module.h"
#include "cr_servo_module.h"
#include "timer.h"
#include "math.h"
#include "printf.h"
#include "malloc.h"

/* internally data concerning information about the car */
static  int wheel_base_mm; // distance between wheels, measured in  mm
static  int wheel_circumference_mm; //measured in mm

/* shimmy constants, configures shimmy unit to be equal to distance betwee
 * line sensors
 * 
 * These values need to be calibrated for each car
 */
static const unsigned int SHIMMY_ANGLE = 15;
static const unsigned int SHIMMY_FORWARD_DISTANCE_CM = 4;
//move back (move back cos(SHIMMY ANGLE) * SHIMMY_FORWARD_DISTANCE
static const unsigned int SHIMMY_BACKWARDS_DISTANCE_CM = 4;

/* for updating angles */
/* I don't think I use this */
static const unsigned int MAX_ANGLE_TRIES = 20;

static wheel * left_wheel;
static wheel * right_wheel;

/* internally kept motor information
 *
 * Absolute position = motor_rotations*360 + motor_relative_angle
 *
 * negative angle example: -30 degrees would be -1 rotations and position of
 * 330 (-360 + 330 = -30).
 */
struct wheel{
    int rotations; //from -infinity to positive infinity
    int relative_angle; //from 0 to 360.
    unsigned int input_pin; //for reading angle
    cr_servo * motor; //for sending outputs
    int forwards_throttle;
    int backwards_throttle;
    int previous_angle; //to help us update wheel positions
};

/* a helper to filter through angles */
static int get_angle(wheel * wheel){
  int raw = pwm_input_get_angle(wheel->input_pin);
  while(raw >= 400){ //make sure it's not the invalid 10000 data point                                  
    raw = pwm_input_get_angle(wheel->input_pin);
  }
  return raw;
}

/* internal helper functions which needs to be called very often, whenever there is wheel movement.
 * Ideally, this would be called on a tiemr interrupt schedule, once every 20 ms maybe, but
 * I am not doing that for now...
 *
 * Wheel1's (left wheel) angles are negated, so that it's positive direciton is forwards                 
 *
 * does a small check to make sure the angles are valid
 */
static void update_wheel_positions(){
  left_wheel->previous_angle = left_wheel->relative_angle;
  left_wheel->relative_angle = -1*get_angle(left_wheel);

  if(left_wheel->relative_angle < -1*350 && left_wheel->previous_angle > -1*10){
    left_wheel->rotations++;
  }else if(left_wheel->relative_angle > -1*10 && left_wheel->previous_angle < -1*350){
    left_wheel->rotations--;
  }

  right_wheel->previous_angle = right_wheel->relative_angle;
  right_wheel->relative_angle = get_angle(right_wheel);

  if(right_wheel->relative_angle > 350 && right_wheel->previous_angle < 10){
    right_wheel->rotations--;
  }else if(right_wheel->relative_angle < 10 && right_wheel->previous_angle > 350){
    right_wheel->rotations++;
  }
}

static void motor_set_throttle(wheel * wheel, int throttle){
    cr_servo_go_to_throttle(wheel->motor, throttle);
}

/* this function is really ugly because some info, like the servo info, I already have set
 * but other info, like wheelbase, I let the user set
 */
void car_control_module_init(unsigned int input1, unsigned int input2, unsigned int output1,
			     unsigned int output2, unsigned int whl_base, unsigned int whl_crfnc){
  pwm_input_init();
  cr_servo_module_init(); //wow this inconsistency hurts...
  left_wheel = malloc(sizeof(wheel));
  right_wheel = malloc(sizeof(wheel));

  //setup pwm inputs
  left_wheel->input_pin = input1;
  right_wheel->input_pin = input2;

  pwm_add_input(left_wheel->input_pin);
  pwm_add_input(right_wheel->input_pin);

  //setup cr servo outputs
  left_wheel->motor = cr_servo_new(output1);
  right_wheel->motor = cr_servo_new(output2);

  cr_servo_auto_setup(left_wheel->motor, 1503, 1265, 1741); //may be incorrect values
  cr_servo_auto_setup(right_wheel->motor, 1509, 1286, 1732);

  left_wheel->forwards_throttle = 22; //default throttles
  right_wheel->forwards_throttle = -24; //these values need to be calibrated for each car

  left_wheel->backwards_throttle = -23; //prevous -21, worked to go backwards
  right_wheel->backwards_throttle = 23; //previous 20

  //update internal positioning/info
  wheel_base_mm = whl_base; //current wheelbase is 96 mm
  wheel_circumference_mm = whl_crfnc; //current wheel diameter is 188.5

  left_wheel->rotations = 0;
  right_wheel->rotations = 0;

  timer_delay_ms(100);

  left_wheel->relative_angle = get_angle(left_wheel); //used get_angle_average before, screwed thigns up
  right_wheel->relative_angle = get_angle(right_wheel);

  left_wheel->previous_angle = left_wheel->relative_angle;
  right_wheel->previous_angle = right_wheel->relative_angle;
}

int get_wheel_angle(wheel * wheel){
  return wheel->rotations * 360 + wheel->relative_angle;
}
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

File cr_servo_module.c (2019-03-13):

#include "cr_servo_module.h"
#include "pwm_output_module.h"
#include "printf.h"
#include "uart.h"
#include "timer.h"
#include "malloc.h"

/* default constants */
const unsigned int CR_DEFAULT_THRESHOLD = 1500;  
const unsigned int MAX_CR_SERVO_THRESHOLD = 3000;
const unsigned int MIN_CR_SERVO_THRESHOLD = 0;

struct cr_servo_motor{
  unsigned int pin;
  unsigned int current_threshold;
  int current_throttle; //goes from -100 to 100
  unsigned int max_threshold;
  unsigned int min_threshold;
  unsigned int threshold_range;
  unsigned int center_threshold; //everything should be symmetric around this value. 
};

/* should do same checks as in servo module */
static int threshold_to_throttle(cr_servo *cr_servo, unsigned int threshold){
  int relative_threshold = threshold - cr_servo->min_threshold;
  return (relative_threshold - cr_servo->center_threshold) * 100 / cr_servo->threshold_range;
}

static unsigned int throttle_to_threshold(cr_servo *cr_servo, int throttle){
  return ((100 + throttle) * cr_servo->threshold_range / 200) + cr_servo->min_threshold; 
}

void cr_servo_module_init(){
  pwm_output_init(); //is it bad that I call this like 50 times?
}

cr_servo *cr_servo_new(unsigned int pin){
  cr_servo * cr_srvo = malloc(sizeof(struct cr_servo_motor));
  cr_srvo->pin = pin;

  /* default cr_servo setup */
  cr_srvo->current_threshold = CR_DEFAULT_THRESHOLD;
  cr_srvo->center_threshold = CR_DEFAULT_THRESHOLD;
  cr_srvo->max_threshold = 1600;
  cr_srvo->min_threshold = 1400;
  cr_srvo->threshold_range = 200;
  cr_srvo->current_throttle = threshold_to_throttle(cr_srvo, cr_srvo->current_threshold);

  pwm_add_output(pin, cr_srvo->current_threshold);

  return cr_srvo;
}

/* should probably functionally decompose, but I'm also lazy */
void cr_servo_setup(cr_servo *cr_servo){
  printf("Beginning continuous rotation servo setup\n");

  /* first find servo center */
  printf("First, let's find the center of our throttle\n");
  unsigned int min_center_threshold = CR_DEFAULT_THRESHOLD;
  cr_servo->current_threshold = min_center_threshold;
  cr_servo_write_threshold(cr_servo);

  printf("Is the servo moving? (y/n)\n");

  char user_response = uart_getchar();

  /* this section is if the cr servo isn't centered near 1500. Definitely need to make solution to this
   * a lot neater than it is currently 
   */
  if(user_response == 'y'){
    min_center_threshold = 1450;
    cr_servo->current_threshold = min_center_threshold;
    cr_servo_write_threshold(cr_servo);
    printf("is the servo moving? (y/n)\n");
    user_response = uart_getchar();
    if(user_response == 'y'){
      min_center_threshold = 1550;
      cr_servo->current_threshold = min_center_threshold;
      cr_servo_write_threshold(cr_servo);
      printf("is the servo moving? (y/n)\n");
      user_response = uart_getchar();
    }
  }

  /*loop until we've found the min_center_threshold */
  while(user_response != 'y'){
    min_center_threshold = min_center_threshold - 1;
    cr_servo->current_threshold = min_center_threshold;
    printf("setting threshold to %d\n", min_center_threshold);
    cr_servo_write_threshold(cr_servo);
    printf("Is the servo moving? (y/n)\n");
    user_response = uart_getchar();
  }

  printf("ok now, again: \n");

  unsigned int max_center_threshold = CR_DEFAULT_THRESHOLD;
  cr_servo->current_threshold = max_center_threshold;
  cr_servo_write_threshold(cr_servo);

  printf("Is the servo moving? (y/n)\n");
  user_response = uart_getchar();

  /* loop until we've found the max_center_threshold */
  while(user_response != 'y'){
    max_center_threshold = max_center_threshold + 1;
    cr_servo->current_threshold = max_center_threshold;
    printf("setting threshold to %d\n", max_center_threshold);
    cr_servo_write_threshold(cr_servo);
    printf("Is the servo moving? (y/n)\n");
    user_response = uart_getchar();
  }

  cr_servo->center_threshold = (max_center_threshold + min_center_threshold)/2;

  /* now find max / min throttle (since symmetric, only need to find one */
  printf("Now we will find the max/min throttles \n");

  unsigned int min_threshold = min_center_threshold;
  cr_servo->current_threshold = min_threshold;
  cr_servo_write_threshold(cr_servo);

  user_response = 'n';

  while(user_response != 'y'){
    min_threshold = min_threshold - 10;
    if(min_threshold <= MIN_CR_SERVO_THRESHOLD){
      min_threshold = MIN_CR_SERVO_THRESHOLD;
      user_response = 'y';
    }
    cr_servo->current_threshold = min_threshold;
    cr_servo_write_threshold(cr_servo);
    printf("setting threshold to %d \n", min_threshold);
    cr_servo_write_threshold(cr_servo);
    printf("have we reached the max/min throttle speed?\n");
    user_response = uart_getchar();
  }

  /* set cr_servo values */
  cr_servo->min_threshold = min_threshold;
  unsigned int threshold_range = (cr_servo->center_threshold - min_threshold)*2;
  cr_servo->threshold_range = threshold_range;
  cr_servo->max_threshold = cr_servo->center_threshold + threshold_range/2;
  cr_servo_go_to_throttle(cr_servo, 0);

  /* print results */
  printf("For reference: \n");
  printf("Center threshold: %d\n", cr_servo->center_threshold);
  printf("Min threshold: %d\n", cr_servo->min_threshold);
  printf("Max threshold: %d\n", cr_servo->max_threshold);
}

void cr_servo_auto_setup(cr_servo *cr_servo, unsigned int center_threshold, unsigned int min_threshold,
			 unsigned int max_threshold){
  cr_servo->center_threshold = center_threshold;
  cr_servo->min_threshold = min_threshold;
  cr_servo->max_threshold = max_threshold;
  cr_servo->threshold_range = max_threshold - min_threshold;
  cr_servo_go_to_throttle(cr_servo, 0);
}

/* sets fields internally and also calls to write threshold to set the throttle */
int cr_servo_go_to_throttle(cr_servo *cr_servo, int throttle){
  unsigned int threshold = throttle_to_threshold(cr_servo, throttle);
  cr_servo->current_throttle = throttle;
  cr_servo->current_threshold = threshold;
  return cr_servo_write_threshold(cr_servo);
  /* same problem with this implementation as with servo_go_to_angle */
}

/* should probably do error checking */
int cr_servo_write_threshold(cr_servo *cr_servo){
  pwm_change_threshold(cr_servo->pin, cr_servo->current_threshold);
  return 1;
}

int get_cr_servo_throttle(cr_servo *cr_servo){
  return cr_servo->current_throttle;
}

unsigned int get_cr_servo_threshold(cr_servo *cr_servo){
  return cr_servo->current_threshold;
}

void test_cr_servo_module(unsigned int pin){
  printf("Beginning cr servo module test\n");
  cr_servo_module_init();

  cr_servo * my_cr_servo = cr_servo_new(pin);

  cr_servo_setup(my_cr_servo);

  int throttle = 0;

  while(1){
    while(throttle < 100){
      cr_servo_go_to_throttle(my_cr_servo, throttle);
      throttle++;
      timer_delay_ms(75);
    }
    while(throttle > -100){
      cr_servo_go_to_throttle(my_cr_servo, throttle);
      throttle--;
      timer_delay_ms(75);
    }
  }
}

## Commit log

2019-03-06 updated for line follower sensor to keep track of position
2019-03-06 progress on basic ultrasonic measuring & added ultrasonic source to proposal.md
2019-03-06 buggy ultrasonic distance sensor code
    [ultrasonic_module.c]
2019-03-06 working basic ultrasonic module
2019-03-06 working ultrasonic module. Realized that I don't need interrupts for this probably
2019-03-06 cleaned up the ultrasonic module a bit
2019-03-06 initial commit of pwm output module
2019-03-06 added servo pwm signal links
2019-03-06 initial commit of pwm output module. wrote first version of all code, have not tested it
2019-03-06 tried testing pwm outputs, however, it seems like my interrupt handler is not running. I will check it out tomorrow. Good night.
2019-03-07 first commit of pwm input reading module
2019-03-07 realized that my current implementation of pwm input isn't as I thought it was. will probably have to integrate it into the pwm_output timer interrupt model
2019-03-07 first commit of servo module, which allows for the creation and control of servo objects
2019-03-07 worked on pwm input. It was literally working perfectly a while ago, but it randomly stopped working. Something with the gpio event detection is not working as expected
    [main.c, pwm_input_module.c]
2019-03-07 I found it. the grounds need to be commnected to the whole system
2019-03-08 servo is working
2019-03-08 tried to make some major restructrual changes to pwm output. Not using a counter anymore, instead a big interrupt block
2019-03-08 tested with servos. it works
2019-03-08 PWM IO works for a single servo. Not for two yet though
2019-03-08 works, execpt uart. Also servo is not getting full range, so I'll edit some things in pwm output
2019-03-08 Added more range to pwm outputs
2019-03-09 got rid of error messages
    [main.c, servo_module.c]
2019-03-09 added a comment that notes a potential error
    [servo_module.c]
2019-03-09 allowed for user to setup servos
2019-03-09 first implementation of continuous rotation servo module complete. Need to debug and test
2019-03-09 got rid of error messages/warnings
    [cr_servo_module.c]
2019-03-09 created first outline of car control module, which combines the continuous rotation servos with the feedback line to create accurate movement control of the car
2019-03-09 added function prototypes to control the throttle the car runs at
2019-03-09 CAD files for 3D printed chassis
    [Chassis_Bottom.stl, Chassis_Top.stl]
2019-03-10 feedback servos are kind of working, but really buggy cause they're twitchy
    [car_control_module.c, main.c]
2019-03-10 slipping seems to be less common now, but definitely need to rewrite get_angle code in input module as well as update_angle code in car control to make sure everything is kosher
    [car_control_module.c, pwm_input_module.c]
2019-03-10 added function prototype for test function
2019-03-10 moved cr servo test function to the cr servo module files
2019-03-10 moved servo module test function to servo module
2019-03-10 fixed a compiler issue
    [line_follower_module.c, main.c]
2019-03-10 wrote all functions, but line follower not currently working
2019-03-10 added in more friction fits and attaching area for line follower module
    [updated_bottom_chassis.stl]
2019-03-10 recorded physical data about wheel base/circumference. Also fixed compiler issues
    [car_control_module.c]
2019-03-10 fixed minor big in turn()
    [car_control_module.c]
2019-03-11 updated pwm input angle measurements
2019-03-12 line follower no longer working
    [line_follower_module.c]
2019-03-12 I seem to have fixed the issues with skipping rotations
    [car_control_module.c]
2019-03-12 works well, only problem is that it's possible (hopefully rare) for the movement to glitch out and get stuck
    [car_control_module.c]
2019-03-12 made ultrasonic module compatible with pwm interrupts
2019-03-12 trying to get rid of slipping wheels
    [car_control_module.c]
2019-03-12 trying to fix rotation slipping
    [car_control_module.c, main.c, pwm_input_module.c]
2019-03-13 made angle reading consistent by carefully timing angle read measurements with pwm output itnerrupts
2019-03-13 implemented turning. Works well, with one rare glitch that I will fix
    [car_control_module.c]
2019-03-13 I think I fixed the bug where it continually goes forward. Need to check
    [car_control_module.c]
2019-03-13 car control works nicely. Just need to update wheelbase/wheel circumference, backwards and forwards throttles for each wheel to fine tune motions to be extra precise
2019-03-13 a better version of the bottom chassis
    [better_bottom_chassis.stl]
2019-03-13 fixed shimmy_left and turning in positive angles
    [car_control_module.c]
2019-03-13 configured shimmying so a single shimmy shimmies the distance between line follower sensors
2019-03-13 added getter functions for wheelbase/wheelcircumference/sensordistance
2019-03-14 fixed compiler issues and experimented with line sensing
    [main.c, pi_rat_sensing_module.c]
2019-03-14 Added a comment that points out a potential issue with the program
    [line_follower_module.c, main.c]
2019-03-14 wall sensing is broken right now. It's being held up somewere in get_ultrasonic_mean
    [main.c, pi_rat_sensing_module.c]
2019-03-14 fixed ultrasonic big
2019-03-14 calibrated the wheel circumference. Working value is 197 mm
2019-03-15 fixed overcall of pwm_output_init as well as testing line correction
    [car_control_module.c, main.c, servo_module.c]
2019-03-15 calibrating constants
2019-03-15 calibrated shimmying. Also, my right and left are switched lol
2019-03-15 fixed error where angle wasn't being corrected
    [car_control_module.c]
2019-03-15 cleaned up debugging printf statements
2019-03-15 maze wall parts. Will laser cut out of 1/8th duron. Parts are designed to hold walls which are made out of 1/8th thick cardboard. Will be placed on maze to create moveable walls
    [8x pi rat maze wall plates.dxf, pi rat maze top:bottom plate.dxf]
2019-03-15 stl file versions of the duron laser cut parts, with 1/8th inch thickness. For a 4x4 maze, will have 18 (9*2) of the bottom/top plates and 96 (4*2*3 + 9*2*4) of the wall plates
    [3d wall plate pi rat maze.stl, pi rat maze bottom:top plate 3d.stl]
2019-03-18 the reason ultrasonic wans't working is because power got unplugged
2019-03-18 was able to wander through the maze! My left and right turning are reversed lol. Also sometimes the line correction gets messed up and over corrects / in correctly corrects. And finally, the pi rat d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
    [pi_rat_sensing_module.c]
2019-03-18 fixed right / left turn reversal
    [pi_rat_sensing_module.c]
2019-03-19 cleaned up some stuff as well as got rid of compiler errors
    [main.c]
2019-03-19 increased angle per sensor--over correcting is better than undercorrecting in this scenario
2019-03-19 wrote first draft of the update maze function. it is currently super ugly and I don't knwo if it works
2019-03-19 added function prototype for get_bearing
2019-03-19 testing new movement correction as well as added a comment on a detail for movement correction that I will tend to later if I feel like it
    [main.c]
2019-03-19 the direciton change function works now. However, I think my right and left may be reversed (which is confusing me because it seems to be working in the maze solving? Perhaps the ultrasonic wall dete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
2019-03-19 fixed error in reversal of left/right walls
    [main.c, pi_rat_sensing_module.c]
2019-03-20 nevermind, turns out what I thought was a bug was just me printing out things in a disorganized fashion. Data structure works now
2019-03-20 the maze solver program makes the wheels turn. Unsure if it does it in the right way, though, because I've yet to test it
2019-03-20 right now the program solves the maze, just really inefficiently. There's always a bias to go left first, then up, then right and finally down. However, this includes paths which it's already explore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
    [main.c]
2019-03-20 I found the bug! The rats maze position wasn't udpated often enough / at the right time
    [main.c, pi_rat_sensing_module.c]
2019-03-20 cleaned up some comments and debugging print statements
2019-03-20 got rid of more debugging print statemnts & extraneous comments
2019-03-21 fixed a bug I introduced with position updating
    [main.c, pi_rat_sensing_module.c]
2019-03-21 generalized the maze solver so it doesn't need a final destination, and can instead search the maze for an opening to the outside
    [main.c]
2019-03-21 added board reset function
2019-03-21 added a button reset
    [main.c]
2019-03-25 fixed the bug that messed the demo up
    [main.c]
